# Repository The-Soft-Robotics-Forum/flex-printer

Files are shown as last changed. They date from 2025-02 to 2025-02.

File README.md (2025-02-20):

# Flex Printer

The Flex Printer is an open-source project aimed at solving the key print reliability difficulties associated with printing ultra-flexible elastomers (i.e. shore hardness of around 80A and below). It is based on the [Voron 0.2](https://github.com/VoronDesign/Voron-0) frame and motion system, but has been heavily modified, and stripped down to remove unnecessary parts; the resulting assembly is much easier to build and use, especially for newcomers to the field.

The project is aimed at providing a democratised platform for carrying out research in soft robotics involving the printing of soft elastomers (e.g. for fluidic soft robots).
The printer can be built for less than $500, with the total assembly time estimated at 1-3 days for first-time users (and under 1 day for those with prior experience).

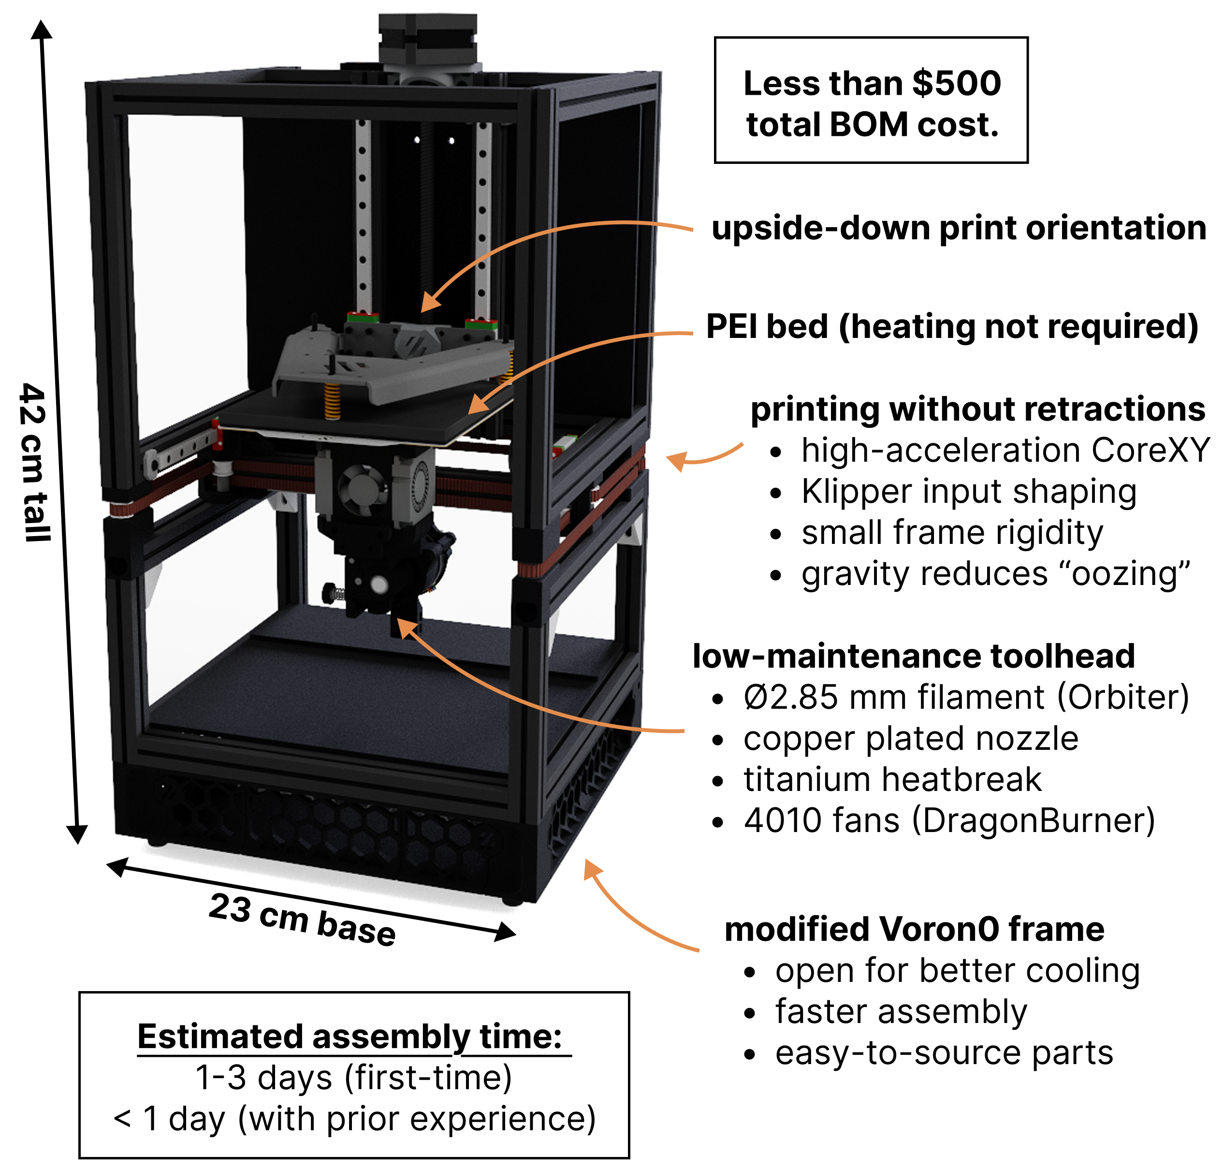
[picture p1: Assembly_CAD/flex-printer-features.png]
The key features of the Flex Printing platform


## Table of Contents
* [Overarching philosophy](#overarching-philosphy)
* [Key features](#key-features)
* [Printing impossible geometries](#printing-previosly-unfeasible-geometries)
* [Getting started](#getting-started)
* [Join the official Discord channel](#join-the-official-discord-channel)
* [How to contribute](#how-to-contribute)

## Overarching philosophy
The original Voron printers are very fun to build, but can be an arduous process for first-time builders; it is a platform designed primarily with hobbyists in mind. The Flex Printer has been optimised to simplify the assembly and usage of the printer as much as possible. The guidance provided in this repository aims to prevent future users of the platform from having the face the same challenges that the authors had to face when building Voron printers. The project follows a Keep It Simple, Stupid (KISS) philosophy, omitting decorative elements and any parts deemed unnecessary. These can, of course, be added back by the users to customise their builds.

## Key features

- Upside-down print orientation
    - Stabilises thin membranes during printing, and helps to keep them airtight (key for printing fluidic soft robots).
    - Allows to print arbitrarily tall slender structures (such as walls and columns). It is now possible to print geometries which previously would have collapsed under their own weight.
    - Enables better bridging and minimises the risk of blockage of fluidic channels (enabling to build more tightly integrated fluidic architectures).
    - Enables to suspend parts on thin strands of filament ("aero supports"), and print parts in virtually any print orientation.
- The printer can print parts in virtually any orientation
    - (Using "aero" support, as explained in the previous point).
    - Unlocks possibilities for creating entirely new types of fluidic machines, soft robots, and metamaterials.
- Low-maintenance, modified extruder
    - Use of 2.85 mm filament, which is 7 times harder to buckle than 1.75 mm.
    - Eliminates the issue of flexible filament tangling itself around extruder gears.
    - The larger cross section allows to generate more force, and gives more control over how the filament is pushed out of the nozzle.
    - Increased maximum printing speeds.
    - Copper-plated nozzle and titanium alloy heatbreak minimise the risk of clogged nozzles.
- Heat bed completely removed to simplify assembly, and operation
    - TPU provides excellent adhesion to the PEI textured sheet, even in the upside-down orientation.
- Open-frame design
    - The lack of enclosure allows for better cooling and significantly simplifies the assembly.
- Compact and portable
    - The printer fits on any desktop (42 x 23 x 23 cm footprint).
    - It can be easily transported, and used even at remote locations, which unlocks new applications.
    - The 120x120x120 mm build volume is sufficient given the current scale of fluidic soft systems. Future development may involve the creation of larger printer size variants.
- Printing without retractions
    - Printing upside down minimises filament oozing.
    - Printing at high accelerations and travel speeds minimises the need for retraction; made possible through CoreXY + Klipper input shaping + small rigid frame. 

## Printing previosly unfeasible geometries
[![Demonstration of printer capabilities]()](https://vimeo.com/1057922438/d0713f3f35)

## Getting started
- Follow the part sourcing guide in the [BOM_Sourcing_Guide](https://github.com/The-Soft-Robotics-Forum/flex-printer/tree/main/BOM_Sourcing_Guide) folder to procure the parts needed to build the printer.
- If your BOM doesn't include all of the required parts, print the remaining ones using the resources available in the [Print_These_Parts](https://github.com/The-Soft-Robotics-Forum/flex-printer/tree/main/Print_These_Parts) folder.
- Follow the build instructions in the [Build_Instructions](https://github.com/The-Soft-Robotics-Forum/flex-printer/tree/main/Build_Instructions) folder to build the printer and get it ready for printing your first parts.
- Visit the [Fluidic Machine Bestiary](https://github.com/The-Soft-Robotics-Forum/fluidic-machine-bestiary) for a repository of ready-to-print monolithic robots. The Bestiary also contains an expanding library of fluidic control, actuator, and sensor components that use can use to build your own, entirely new, soft robots.

## Join the official Discord channel
We have set up a dedicated [Discord channel](https://discord.gg/4RNmUT7A5G) on the Soft Robotics Forum server. It's a great way to ask for help and advice when assembling and using the printer, as well as to connect with other members of the community, and start contributing your own ideas to the project.

## How to contribute
This is a beginner guide for forking github repositories and contributing to project. If you have prior experience, skip to [Step 6](#step-6:-pull-request). If you plan to contribute to the project, keep in mind that it is under the same license as the standard Voron printers; please see the LICENSE file for full details.
### Step 1: Fork the repo
1. Click the "Fork" button in the top-right corner of the page - [1](https://www.freecodecamp.org/news/how-to-fork-a-github-repository/).
2. Chose where to fork the repository.
### Step 2: Clone your forked repo
1. Go to your forked repo and copy the URL that appears when the green code button is clicked. 
2. Open a terminal on your computer and run `git clone [URL]` [2](https://www.gitkraken.com/learn/git/problems/github-how-to-fork).
### Step 3: Create a branch 
1. Navigate to your recently cloned repo on your pc via terminal.
2. `git checkout -b [NEW_BRANCH_NAME]` where new_branch_name is the name you wish to give your branch.
### Step 4: Make changes 
1. Make your desired changes to the part files keep note of the voron naming scheme and be consistent.
2. Run `git add .`
3. Run `git commit -m "a detailed message of the changes you have made"`
### Step 5: Push changes and create a pull request
1. `git push origin [NEW_BRANCH_NAME]`
2. Go to your fork on the github website and select compare and pull request.
3. Fill in the pull request details.
### Step 6: Pull request
- Provide a clear and concise title for the pull request.
- Include a detailed description of the part changes you have made and why.
	- If you have introduced new parts make sure the naming is consistent with the in place naming scheme.
	- If you have introduced new hardware please provide a BOM for this.

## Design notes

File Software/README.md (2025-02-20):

# FLEX PRINTER ORCA INSTALL GUIDE 

## Step 1 
- Install the latest release of OrcaSlicer from their github releases page if you have not done so: [Orca Github](https://github.com/SoftFever/OrcaSlicer/releases_)

## Step 2 
- Select the preview tab, go to printer drop down, and select `Select/Remove printers(system presets)`
    - if this is your first install of orcaslicer the page will likely look a little different, but the steps are much the same 

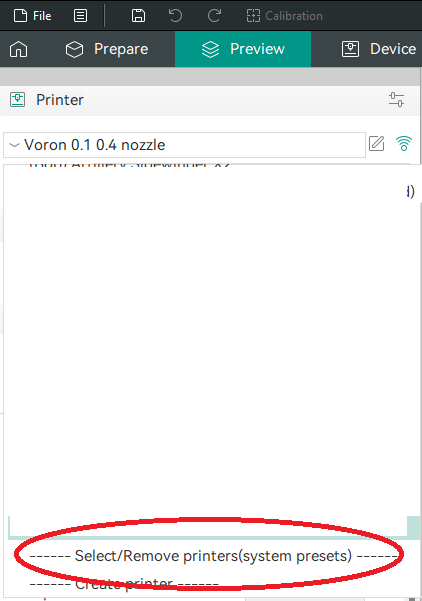
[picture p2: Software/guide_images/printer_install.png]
printer


## Step 3 
- Enter `Voron` into the search 
- Select the Voron 0.1 with 0.4 mm nozzle (or whatever nozzle size you have installed) 
- Press Confirm

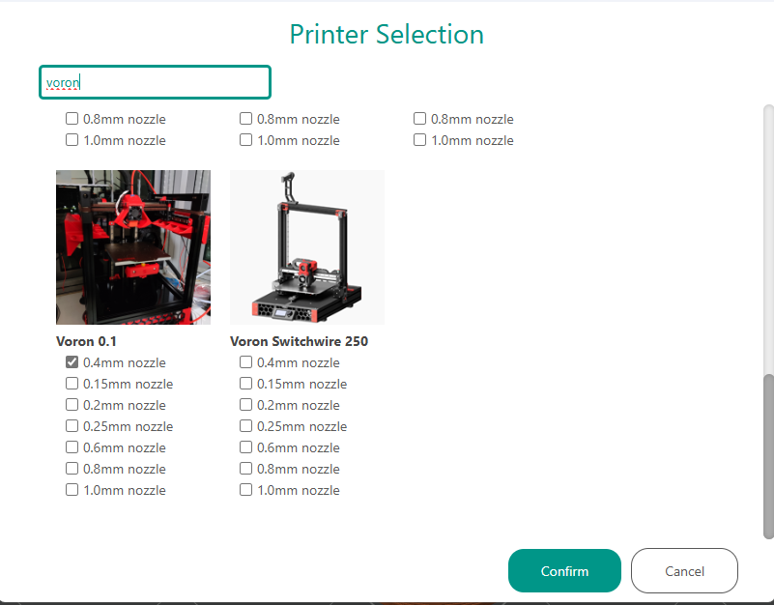
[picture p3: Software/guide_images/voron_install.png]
voron


## Step 4
- Ensure the Voron is selected in the drop down
- In the top left of the screen go to file/import/import configs...
- Locate the `orca_slicer_presets.orca_printer` file available [here](https://github.com/The-Soft-Robotics-Forum/flex-printer/blob/main/Software/orca_slicer_presets.orca_printer)
- This will make the Flex Printer presets available as options on the voron printer model 

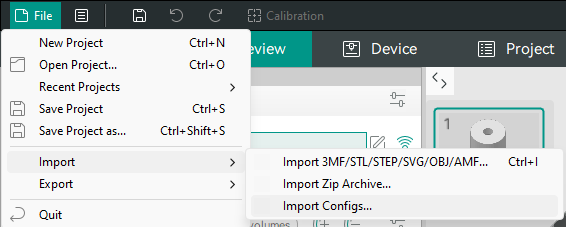
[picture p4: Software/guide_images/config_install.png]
config


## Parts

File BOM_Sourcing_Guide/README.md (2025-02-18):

# Bill of Materials (BOM) and sourcing guide
The included spreadsheet file contains our recommendations for the parts to purchase for the build. We will provide a couple of alternatives, as well as Aliexpress links so that they can be easily sourced globally. Note the pricess fluctuate rapidly on Ali, there are also variations in exchange rates. You might be able to find a better deal from one of the local suppliers on your country (e.g. [OneTwo3D](https://www.onetwo3d.co.uk/) in the UK, or [3DJake](https://www.3djake.uk/) in Germany & rest of EU).

### Finding the best BOM option for you
One of the easiest ways to source the printer parts is to actually buy one of the pre-made kits from brands like LDO, Siboor, Formbot, FYSETC. Note that when ordering a kit, you will be throwing away half of the parts since we don't need them, but you will also have more spares of others. Some kits come with a surplus of the printed parts, so this might be the option for you if you don't have another printer to print them.

The ranking of differences in quality between these brands is a subject of widespread discussion amongst Voron community members, but the general consensus appears to be that LDO is by far the highest quality, Siboor is OK and much cheaper, Formbot and FYSETC are the cheapest, but can be hit or miss, i.e. you might get lower quality parts, with worse tolerances. Lower part quality might limit your machine's performance and reliability slightly, but comes with the benefit of a lower price point.

Buying a Siboor/Formbot/FYSETC kit + any remaining parts is probably the easiest way to get below the $500 price point. One of the goals of the project is to further refine this sourcing process to make it as easy as possible; this might involve a custom kit specifically for this printer, or some new custom parts which simplify the assembly and reduce the cost even further.

A good middle ground for now can be sourcing LDO parts for the components which affect the performance the most (in order of importance: the linear rails, motors, frame extrusions, nozzles), though this might result in going slightly above the $500 price point depending on where you are ordering from, the fluctuating prices and currency exchange rates, etc.

### Electronics
The default for electronics is using a Raspberry Pi3B/3B+ or newer, but you could also use a Pi Zero 2W to further reduce the price point; this does come with some caveats though, and the regular Pi makes it easier to add further addons like webcams using USB, so we recommend this option. The are also boards that remove the need for a separate Pi running Klipper + MCU board, like the Fly Gemini 3.0 board with which some kits like Siboor come packaged with. This can be convenient, but OP has seen that there can sometimes be mysterious issues with these boards (or they work perfectly fine...). The Pi + SKR Pico combo is the safe choice if you want to make sure you don't run into issues later.

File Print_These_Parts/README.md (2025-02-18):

# Printed part directory
If you don't decide to build the printer using a kit that comes with all of the printed (or CNC'd) parts, you will need to print them yourself. Since the assembly has been heavily simplified, there aren't that many parts left to print.

The "Ready_To_Print_Prearranged" folder comes with preset plates that you can load into your slicer, and go. The .3mf file also includes the default recommended settings for FDM:
* 0.2mm layer height
* 0.4mm forced extrusion width
* Infill types: either grid, gyroid, honeycomb, triangle or cubic
* 40% infill percentage
* 4 perimeters (walls)
* 5 top/bottom solid layers.

For the material, the recommendation is always ABS/ASA as other materials like PLA can degrade and crack, especially when under temperature. Since we are not using an enclosure and heated bed, you could possibly get away with it, but we highly recommend sticking with ABS/ASA to avoid issues.

You can also use the Voron community Print It Forward (PIF) scheme to pay community members located near you to print and ship the parts to you. To find out more, visit https://pif.voron.dev/

# Part file naming guide
The "Individual_STL" files contains all the separate STL files, in case you want to slice and print them separately.

**QUANTITY REQUIRED**

*Thumb_Nut_x3.stl*  
Any file that ends with “_x#” is telling you the quantity of that part required to build the machine.

**FYI: ACCENT COLOR**

*[a]_Tensioner_Knob_x2.stl*  
The original Voron files use the "[\a]" prefix to indicate the part should be printed with a coloured accent (and "[\c]" for clear parts). This is unnecessary, and just complicates the overall build process, so we recommend printing all parts in one colour. Noting it here to indicate what it means in the original Voron naming scheme that you might notice being used if reusing parts from other repositories.

# Optional files
The "[\Optional]_Extra_or_Alternative_Parts" folder contains optional addons, adapters for alternative electronics boards, etc. You do not need to print these for the stock build.

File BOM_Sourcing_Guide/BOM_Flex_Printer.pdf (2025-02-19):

Category | Item | Qty. Price (GBP) Subtotal (GBP) | Link | Comments
Formbot Kit Kit options Siboor Kit FYSETC Kit | 1 0 0 | £275.19 £275.19 £317.92 £0.00 £359.59 £0.00
Aluminum Bed, 120x120x6mm Print bed Kirigami Bed | 0 0 0 | £12.09 £0.00 £5.69 £0.00 £10.18 £0.00
BTT SKR Pico | 0 | £15.24 £0.00
Electronics | Raspberry Pi 3B or newer | 0 | £33.99 | £0.00 | You might be able to source for cheaper elsewhere, or have one lying around. (https://www.aliexpress.com/item/1005005686303304.html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)
| MicroSD Card, 16G or more | 1 | £2.34 | £2.34 | Kit might also include this (https://www.aliexpress.com/item/1005007498193121.html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)
Umbillical PCB | 0 | £10.29 £0.00
Fans 4010 blower fan, dual ball GDSTIME | 2 | £10.69 £21.38
D2F-5 end stop switch | 0 | £0.52 | £0.00 | You can grab spares. (https://www.aliexpress.com/item/1005005204376959.html)
Axial Fan, 3010, 24V | 0 | £7.44 | £0.00 | The kits should have 2 of these, but double check (https://www.aliexpress.com/item/1005001793269882.html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)
Extruder 3.0 mm titanium heatbreak V6 heatsink 3.0 mm Heater + thermistor 2.85 mm drive gear kit TriangleLab | 1 1 1 1 | £4.34 £4.34 £3.24 £3.24 £3.51 £3.51 £13.29 £13.29
Orbiter V1.5 hardware + LDO motor | 0 | £28.79 £0.00
Hotend sock V6 plated copper block trianglelab | 1 1 | £2.16 £2.16 £9.79 £9.79
Power Mains switch | 0 | £1.12 £0.00
Orbiter V1.5 hardware, no motor | 1 | £12.29 | £12.29 | Note the Orbiter 1.5 has a different footprint from the F2.85, so our extruder printed part has a slight spacer to accommodate (https://www.aliexpress.com/item/1005002278201831.html) the injection molded part.
Orbiter F2.85 LDO prebuilt | 0 | £46.59 | £0.00 | The kits come with the stepper motor, but by buying this part you won’t need to print the parts (https://www.aliexpress.com/item/1005002781074910.html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)
LRS-100-24 power supply | 0 | £15.69 | £0.00 | Stock kit comes with 150W or more but we’re not using a heated bed. 100W should be more than enough, but you (https://www.aliexpress.com/item/4000417108777.html) can always get a bigger one.

Other

Siboor Hardware Kit | 0 | £22.59 | £0.00 | This has plenty of spare fasteners as well, but you could use more M3x10 and M3x50 (https://www.aliexpress.com/item/1005004195409464.html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)
M3x10 BHCS (50 pcs) | 1 | £1.15 | £1.15
M3x50 (any hex, 10pcs) | 1 | £1.60 | £1.60
6mm gates belt (4M length) | 0 | £7.82 | £0.00 | You can grab longer length to have spares (https://www.aliexpress.com/item/32853559638.html)
Corner brackets x 4 | 1 | £4.39 | £4.39 | For fixing bottom third of frame (i.e. former tophat) to the rest of the body. You can also use other fasteners, or print your (https://www.aliexpress.com/item/1005002337390401.html) own attachment.

If not getting a kit

Frame kit | 0 | £43.79 | £0.00 | If you can find the LDO kit somewhere else, it should be high quality. (https://www.aliexpress.com/item/1005004054773766.html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)
T nuts for rails | 0 | £10.49 | £0.00
LDO motor kit | 0 | £60.79 | £0.00
LDO linear rail kit | 0 | £69.95 | £0.00 | Couldn’t find on Ali (https://www.onetwo3d.co.uk/product/voron-0-linear-rail-kit-by-ldo/)
Set of panels (any should do, can procure for much cheaper) | 0 | £19.99 | £0.00 | Couldn’t find on Ali (https://www.onetwo3d.co.uk/product/linneo-voron-0-2-deck-back-panels-acm/)
TOTAL | £354.67

### Legend

Required
Not required
Different options you can opt for https://www.aliexpress.com/item/1005007863277974.html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 https://www.aliexpress.com/item/1005005295642824.html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 https://www.aliexpress.com/item/1005005338161717.html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 https://www.aliexpress.com/item/1005004428776917.html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
Spring Steel Flex Plate, 120x120mm, PEI Textured + smooth | https://www.aliexpress.com/item/1005005551646331.html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 https://www.aliexpress.com/item/1005005913879717.html?spm=a2g0o.order_list.order_list_main.386.24d01802XzWiW8 https://www.aliexpress.com/item/1005005686303304.html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 https://www.aliexpress.com/item/1005006043530249.html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 https://www.aliexpress.com/item/1005007498193121.html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 https://www.aliexpress.com/item/1005004265151654.html?spm=a2g0o.order_list.order_list_main.341.44c2180236tlJw https://www.aliexpress.com/item/1005005204376959.html?spm=a2g0o.order_list.order_list_main.336.44c2180236tlJw https://www.aliexpress.com/item/32799324058.html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 https://www.aliexpress.com/item/1005001793269882.html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 https://www.aliexpress.com/item/4000057995088.html?spm=a2g0o.order_list.order_list_main.360.24d01802XzWiW8 https://www.aliexpress.com/item/1005003064205906.html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 https://www.aliexpress.com/item/32849251623.html?spm=a2g0o.order_detail.order_detail_item.11.29e5f19cB9587U https://www.aliexpress.com/item/32950159362.html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 https://www.aliexpress.com/item/1005002278201831.html?spm=a2g0o.order_list.order_list_main.5.433c1802csn2bN https://www.aliexpress.com/item/1005002278201831.html?spm=a2g0o.order_list.order_list_main.5.433c1802csn2bN https://www.aliexpress.com/item/1005002781074910.html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 https://www.aliexpress.com/item/32916210903.html?spm=a2g0o.order_list.order_list_main.281.44c2180236tlJw https://www.aliexpress.com/item/4000011928654.html?spm=a2g0o.order_list.order_list_main.363.44c2180236tlJw https://www.aliexpress.com/item/1005005173695637.html?spm=a2g0o.order_list.order_list_main.346.44c2180236tlJw https://www.aliexpress.com/item/4000417108777.html?spm=a2g0o.order_list.order_list_main.351.44c2180236tlJw https://www.aliexpress.com/item/1005004195409464.html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 https://www.aliexpress.com/item/1005008064515476.html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 https://www.aliexpress.com/item/4000282775348.html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 https://www.aliexpress.com/item/32853559638.html?spm=a2g0o.order_list.order_list_main.321.44c2180236tlJw https://www.aliexpress.com/item/1005002337390401.html?spm=a2g0o.order_list.order_list_main.301.44c2180236tlJw https://www.aliexpress.com/item/1005004054773766.html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 https://www.aliexpress.com/item/1005007163562504.html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 https://www.aliexpress.com/item/1005004932910282.html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 https://www.onetwo3d.co.uk/product/voron-0-linear-rail-kit-by-ldo/ https://www.onetwo3d.co.uk/product/linneo-voron-0-2-deck-back-panels-acm/

Category | Item | Qty. Price (GBP) Subtotal (GBP) | Link | Comments
Formbot Kit Kit options Siboor Kit FYSETC Kit | 0 0 0 | £275.19 £0.00 £317.92 £0.00 £359.59 £0.00
Aluminum Bed, 120x120x6mm Print bed Kirigami Bed | 1 1 1 | £12.09 £12.09 £5.69 £5.69 £10.18 £10.18
BTT SKR Pico MicroSD Card, 16G or more Umbillical PCB | 1 1 1 | £15.24 £15.24 £2.34 £2.34 £10.29 £10.29
Fans 4010 blower fan, dual ball GDSTIME Axial Fan, 3010, 24V | 2 2 | £10.69 £21.38 £7.44 £14.88
Extruder 3.0 mm titanium heatbreak V6 heatsink 3.0 mm Heater + thermistor | 1 1 1 | £4.34 £4.34 £3.24 £3.24 £3.51 £3.51
2.85 mm drive gear kit TriangleLab | 0 | £13.29 £0.00
Electronics | Raspberry Pi 3B or newer | 1 | £33.99 | £33.99 | You might be able to source for cheaper elsewhere, or have one lying around. (https://www.aliexpress.com/item/1005005686303304.html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)
D2F-5 end stop switch | 1 | £0.52 | £0.52 | You can grab spares. (https://www.aliexpress.com/item/1005005204376959.html)
Orbiter V1.5 hardware, no motor | 0 | £12.29 | £0.00 | Note the Orbiter 1.5 has a different footprint from the F2.85, so our extruder printed part has a slight spacer to accommodate (https://www.aliexpress.com/item/1005002278201831.html) the injection molded part.
Orbiter V1.5 hardware + LDO motor | 0 | £28.79 £0.00
Hotend sock V6 plated copper block trianglelab | 1 1 | £2.16 £2.16 £9.79 £9.79
Power Mains switch | 1 | £1.12 £1.12
M3x10 BHCS (50 pcs) Other M3x50 (any hex, 10pcs) Corner brackets x 4 | 1 1 1 | £1.15 £1.15 £1.60 £1.60 £4.39 £4.39
Orbiter F2.85 LDO prebuilt | 1 | £46.59 | £46.59 | The kits come with the stepper motor, but by buying this part you won’t need to print the parts (https://www.aliexpress.com/item/1005002781074910.html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)
LRS-100-24 power supply | 1 | £15.69 | £15.69 | Stock kit comes with 150W or more but we’re not using a heated bed. 100W should be more than enough, but you (https://www.aliexpress.com/item/4000417108777.html) can always get a bigger one.
Siboor Hardware Kit | 1 | £22.59 | £22.59 | This has plenty of spare fasteners as well, but you could use more M3x10 and M3x50 (https://www.aliexpress.com/item/1005004195409464.html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)
6mm gates belt (4M length) | 1 | £7.82 | £7.82 | You can grab longer length to have spares (https://www.aliexpress.com/item/32853559638.html)

If not getting a kit

Frame kit | 1 | £43.79 | £43.79 | If you can find the LDO kit somewhere else, it should be high quality. (https://www.aliexpress.com/item/1005004054773766.html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)
T nuts for rails | 1 | £10.49 | £10.49
LDO motor kit | 1 | £60.79 | £60.79
LDO linear rail kit | 1 | £69.95 | £69.95 | Couldn’t find on Ali (https://www.onetwo3d.co.uk/product/voron-0-linear-rail-kit-by-ldo/)
Set of panels (any should do, can procure for much cheaper) | 1 | £19.99 | £19.99 | Couldn’t find on Ali (https://www.onetwo3d.co.uk/product/linneo-voron-0-2-deck-back-panels-acm/)
TOTAL | £455.60

### Legend

Required
Not required
Different options you can opt for https://www.aliexpress.com/item/1005007863277974.html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 https://www.aliexpress.com/item/1005005295642824.html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 https://www.aliexpress.com/item/1005005338161717.html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 https://www.aliexpress.com/item/1005004428776917.html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
Spring Steel Flex Plate, 120x120mm, PEI Textured + smooth | https://www.aliexpress.com/item/1005005551646331.html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 https://www.aliexpress.com/item/1005005913879717.html?spm=a2g0o.order_list.order_list_main.386.24d01802XzWiW8 https://www.aliexpress.com/item/1005005686303304.html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 https://www.aliexpress.com/item/1005006043530249.html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 https://www.aliexpress.com/item/1005007498193121.html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 https://www.aliexpress.com/item/1005004265151654.html?spm=a2g0o.order_list.order_list_main.341.44c2180236tlJw https://www.aliexpress.com/item/1005005204376959.html?spm=a2g0o.order_list.order_list_main.336.44c2180236tlJw https://www.aliexpress.com/item/32799324058.html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 https://www.aliexpress.com/item/1005001793269882.html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 https://www.aliexpress.com/item/4000057995088.html?spm=a2g0o.order_list.order_list_main.360.24d01802XzWiW8 https://www.aliexpress.com/item/1005003064205906.html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 https://www.aliexpress.com/item/32849251623.html?spm=a2g0o.order_detail.order_detail_item.11.29e5f19cB9587U https://www.aliexpress.com/item/32950159362.html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 https://www.aliexpress.com/item/1005002278201831.html?spm=a2g0o.order_list.order_list_main.5.433c1802csn2bN https://www.aliexpress.com/item/1005002278201831.html?spm=a2g0o.order_list.order_list_main.5.433c1802csn2bN https://www.aliexpress.com/item/1005002781074910.html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 https://www.aliexpress.com/item/32916210903.html?spm=a2g0o.order_list.order_list_main.281.44c2180236tlJw https://www.aliexpress.com/item/4000011928654.html?spm=a2g0o.order_list.order_list_main.363.44c2180236tlJw https://www.aliexpress.com/item/1005005173695637.html?spm=a2g0o.order_list.order_list_main.346.44c2180236tlJw https://www.aliexpress.com/item/4000417108777.html?spm=a2g0o.order_list.order_list_main.351.44c2180236tlJw https://www.aliexpress.com/item/1005004195409464.html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 https://www.aliexpress.com/item/1005008064515476.html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 https://www.aliexpress.com/item/4000282775348.html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 https://www.aliexpress.com/item/32853559638.html?spm=a2g0o.order_list.order_list_main.321.44c2180236tlJw https://www.aliexpress.com/item/1005002337390401.html?spm=a2g0o.order_list.order_list_main.301.44c2180236tlJw https://www.aliexpress.com/item/1005004054773766.html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 https://www.aliexpress.com/item/1005007163562504.html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 https://www.aliexpress.com/item/1005004932910282.html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 https://www.onetwo3d.co.uk/product/voron-0-linear-rail-kit-by-ldo/ https://www.onetwo3d.co.uk/product/linneo-voron-0-2-deck-back-panels-acm/

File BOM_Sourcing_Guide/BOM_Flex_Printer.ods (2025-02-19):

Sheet: Cheapest (Kit + remaining parts)
Category | Item | Qty. | Price (GBP) | Subtotal (GBP) | Link | Comments
Kit options | Formbot Kit | 1 | £275.19 | £275.19 | https://www.aliexpress.com/item/1005007863277974.html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
 | Siboor Kit | 0 | £317.92 | £0.00 | https://www.aliexpress.com/item/1005005295642824.html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
 | FYSETC Kit | 0 | £359.59 | £0.00 | https://www.aliexpress.com/item/1005005338161717.html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
Print bed | Aluminum Bed, 120x120x6mm | 0 | £12.09 | £0.00 | https://www.aliexpress.com/item/1005004428776917.html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
 | Spring Steel Flex Plate, 120x120mm, PEI Textured + smooth | 0 | £5.69 | £0.00 | https://www.aliexpress.com/item/1005005551646331.html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
 | Kirigami Bed | 0 | £10.18 | £0.00 | https://www.aliexpress.com/item/1005005913879717.html
Electronics | Raspberry Pi 3B or newer | 0 | £33.99 | £0.00 | https://www.aliexpress.com/item/1005005686303304.html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 | You might be able to source for cheaper elsewhere, or have one lying around.
 | BTT SKR Pico | 0 | £15.24 | £0.00 | https://www.aliexpress.com/item/1005006043530249.html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
 | MicroSD Card, 16G or more | 1 | £2.34 | £2.34 | https://www.aliexpress.com/item/1005007498193121.html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 | Kit might also include this
 | Umbillical PCB | 0 | £10.29 | £0.00 | https://www.aliexpress.com/item/1005004265151654.html
 | D2F-5 end stop switch | 0 | £0.52 | £0.00 | https://www.aliexpress.com/item/1005005204376959.html | You can grab spares.
Fans | 4010 blower fan, dual ball GDSTIME | 2 | £10.69 | £21.38 | https://www.aliexpress.com/item/32799324058.html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
 | Axial Fan, 3010, 24V | 0 | £7.44 | £0.00 | https://www.aliexpress.com/item/1005001793269882.html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 | The kits should have 2 of these, but double check
Extruder | 3.0 mm titanium heatbreak | 1 | £4.34 | £4.34 | https://www.aliexpress.com/item/4000057995088.html
 | V6 heatsink 3.0 mm | 1 | £3.24 | £3.24 | https://www.aliexpress.com/item/1005003064205906.html
 | Heater + thermistor | 1 | £3.51 | £3.51 | https://www.aliexpress.com/item/32849251623.html
 | 2.85 mm drive gear kit TriangleLab | 1 | £13.29 | £13.29 | https://www.aliexpress.com/item/32950159362.html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
 | Orbiter V1.5 hardware, no motor | 1 | £12.29 | £12.29 | https://www.aliexpress.com/item/1005002278201831.html | Note the Orbiter 1.5 has a different footprint from the F2.85, so our extruder printed part has a slight spacer to accommodate the injection molded part.
 | Orbiter V1.5 hardware + LDO motor | 0 | £28.79 | £0.00 | https://www.aliexpress.com/item/1005002278201831.html
 | Orbiter F2.85 LDO prebuilt | 0 | £46.59 | £0.00 | https://www.aliexpress.com/item/1005002781074910.html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 | The kits come with the stepper motor, but by buying this part you won’t need to print the parts
 | Hotend sock | 1 | £2.16 | £2.16 | https://www.aliexpress.com/item/32916210903.html
 | V6 plated copper block trianglelab | 1 | £9.79 | £9.79 | https://www.aliexpress.com/item/4000011928654.html
Power | Mains switch | 0 | £1.12 | £0.00 | https://www.aliexpress.com/item/1005005173695637.html
 | LRS-100-24 power supply | 0 | £15.69 | £0.00 | https://www.aliexpress.com/item/4000417108777.html | Stock kit comes with 150W or more but we’re not using a heated bed. 100W should be more than enough, but you can always get a bigger one.
Other | Siboor Hardware Kit | 0 | £22.59 | £0.00 | https://www.aliexpress.com/item/1005004195409464.html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 | This has plenty of spare fasteners as well, but you could use more M3x10 and M3x50
 | M3x10 BHCS (50 pcs) | 1 | £1.15 | £1.15 | https://www.aliexpress.com/item/1005008064515476.html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
 | M3x50 (any hex, 10pcs) | 1 | £1.60 | £1.60 | https://www.aliexpress.com/item/4000282775348.html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
 | 6mm gates belt (4M length) | 0 | £7.82 | £0.00 | https://www.aliexpress.com/item/32853559638.html | You can grab longer length to have spares
 | Corner brackets x 4 | 1 | £4.39 | £4.39 | https://www.aliexpress.com/item/1005002337390401.html | For fixing bottom third of frame (i.e. former tophat) to the rest of the body. You can also use other fasteners, or print your own attachment.
If not getting a kit | Frame kit | 0 | £43.79 | £0.00 | https://www.aliexpress.com/item/1005004054773766.html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 | If you can find the LDO kit somewhere else, it should be high quality.
 | T nuts for rails | 0 | £10.49 | £0.00 | https://www.aliexpress.com/item/1005007163562504.html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
 | LDO motor kit | 0 | £60.79 | £0.00 | https://www.aliexpress.com/item/1005004932910282.html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
 | LDO linear rail kit | 0 | £69.95 | £0.00 | https://www.onetwo3d.co.uk/product/voron-0-linear-rail-kit-by-ldo/ | Couldn’t find on Ali
 | Set of panels (any should do, can procure for much cheaper) | 0 | £19.99 | £0.00 | https://www.onetwo3d.co.uk/product/linneo-voron-0-2-deck-back-panels-acm/ | Couldn’t find on Ali
 |  |  | TOTAL | £354.67
 |  |  | Legend
 |  |  |  | Required
 |  |  |  | Not required
 |  |  |  | Different options you can opt for

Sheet: Upper-mid-range (Non-kit + LDO parts)_2
Category | Item | Qty. | Price (GBP) | Subtotal (GBP) | Link | Comments
Kit options | Formbot Kit | 0 | £275.19 | £0.00 | https://www.aliexpress.com/item/1005007863277974.html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
 | Siboor Kit | 0 | £317.92 | £0.00 | https://www.aliexpress.com/item/1005005295642824.html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
 | FYSETC Kit | 0 | £359.59 | £0.00 | https://www.aliexpress.com/item/1005005338161717.html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
Print bed | Aluminum Bed, 120x120x6mm | 1 | £12.09 | £12.09 | https://www.aliexpress.com/item/1005004428776917.html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
 | Spring Steel Flex Plate, 120x120mm, PEI Textured + smooth | 1 | £5.69 | £5.69 | https://www.aliexpress.com/item/1005005551646331.html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
 | Kirigami Bed | 1 | £10.18 | £10.18 | https://www.aliexpress.com/item/1005005913879717.html
Electronics | Raspberry Pi 3B or newer | 1 | £33.99 | £33.99 | https://www.aliexpress.com/item/1005005686303304.html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 | You might be able to source for cheaper elsewhere, or have one lying around.
 | BTT SKR Pico | 1 | £15.24 | £15.24 | https://www.aliexpress.com/item/1005006043530249.html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
 | MicroSD Card, 16G or more | 1 | £2.34 | £2.34 | https://www.aliexpress.com/item/1005007498193121.html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
 | Umbillical PCB | 1 | £10.29 | £10.29 | https://www.aliexpress.com/item/1005004265151654.html
 | D2F-5 end stop switch | 1 | £0.52 | £0.52 | https://www.aliexpress.com/item/1005005204376959.html | You can grab spares.
Fans | 4010 blower fan, dual ball GDSTIME | 2 | £10.69 | £21.38 | https://www.aliexpress.com/item/32799324058.html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
 | Axial Fan, 3010, 24V | 2 | £7.44 | £14.88 | https://www.aliexpress.com/item/1005001793269882.html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
Extruder | 3.0 mm titanium heatbreak | 1 | £4.34 | £4.34 | https://www.aliexpress.com/item/4000057995088.html
 | V6 heatsink 3.0 mm | 1 | £3.24 | £3.24 | https://www.aliexpress.com/item/1005003064205906.html
 | Heater + thermistor | 1 | £3.51 | £3.51 | https://www.aliexpress.com/item/32849251623.html
 | 2.85 mm drive gear kit TriangleLab | 0 | £13.29 | £0.00 | https://www.aliexpress.com/item/32950159362.html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
 | Orbiter V1.5 hardware, no motor | 0 | £12.29 | £0.00 | https://www.aliexpress.com/item/1005002278201831.html | Note the Orbiter 1.5 has a different footprint from the F2.85, so our extruder printed part has a slight spacer to accommodate the injection molded part.
 | Orbiter V1.5 hardware + LDO motor | 0 | £28.79 | £0.00 | https://www.aliexpress.com/item/1005002278201831.html
 | Orbiter F2.85 LDO prebuilt | 1 | £46.59 | £46.59 | https://www.aliexpress.com/item/1005002781074910.html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 | The kits come with the stepper motor, but by buying this part you won’t need to print the parts
 | Hotend sock | 1 | £2.16 | £2.16 | https://www.aliexpress.com/item/32916210903.html
 | V6 plated copper block trianglelab | 1 | £9.79 | £9.79 | https://www.aliexpress.com/item/4000011928654.html
Power | Mains switch | 1 | £1.12 | £1.12 | https://www.aliexpress.com/item/1005005173695637.html
 | LRS-100-24 power supply | 1 | £15.69 | £15.69 | https://www.aliexpress.com/item/4000417108777.html | Stock kit comes with 150W or more but we’re not using a heated bed. 100W should be more than enough, but you can always get a bigger one.
Other | Siboor Hardware Kit | 1 | £22.59 | £22.59 | https://www.aliexpress.com/item/1005004195409464.html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 | This has plenty of spare fasteners as well, but you could use more M3x10 and M3x50
 | M3x10 BHCS (50 pcs) | 1 | £1.15 | £1.15 | https://www.aliexpress.com/item/1005008064515476.html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
 | M3x50 (any hex, 10pcs) | 1 | £1.60 | £1.60 | https://www.aliexpress.com/item/4000282775348.html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
 | 6mm gates belt (4M length) | 1 | £7.82 | £7.82 | https://www.aliexpress.com/item/32853559638.html | You can grab longer length to have spares
 | Corner brackets x 4 | 1 | £4.39 | £4.39 | https://www.aliexpress.com/item/1005002337390401.html
If not getting a kit | Frame kit | 1 | £43.79 | £43.79 | https://www.aliexpress.com/item/1005004054773766.html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 | If you can find the LDO kit somewhere else, it should be high quality.
 | T nuts for rails | 1 | £10.49 | £10.49 | https://www.aliexpress.com/item/1005007163562504.html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
 | LDO motor kit | 1 | £60.79 | £60.79 | https://www.aliexpress.com/item/1005004932910282.html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
 | LDO linear rail kit | 1 | £69.95 | £69.95 | https://www.onetwo3d.co.uk/product/voron-0-linear-rail-kit-by-ldo/ | Couldn’t find on Ali
 | Set of panels (any should do, can procure for much cheaper) | 1 | £19.99 | £19.99 | https://www.onetwo3d.co.uk/product/linneo-voron-0-2-deck-back-panels-acm/ | Couldn’t find on Ali
 |  |  | TOTAL | £455.60
 |  |  | Legend
 |  |  |  | Required
 |  |  |  | Not required
 |  |  |  | Different options you can opt for

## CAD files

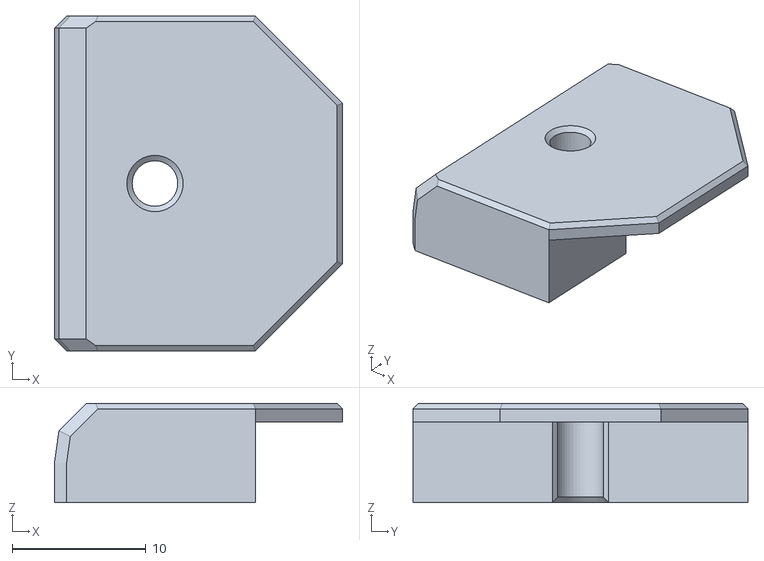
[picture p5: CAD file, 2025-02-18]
Print_These_Parts/Individual_STL/Electronics/Bottom_Panel_Clip_Taller_Longer_x2.stl
21.5 x 25.0 x 7.40

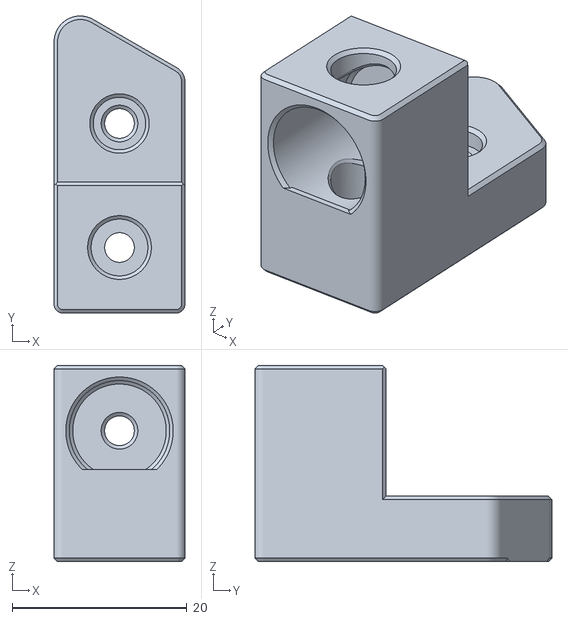
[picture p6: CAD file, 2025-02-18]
Print_These_Parts/Individual_STL/Motion/B_Idler_Upper_x1.stl
15.0 x 34.0 x 22.5

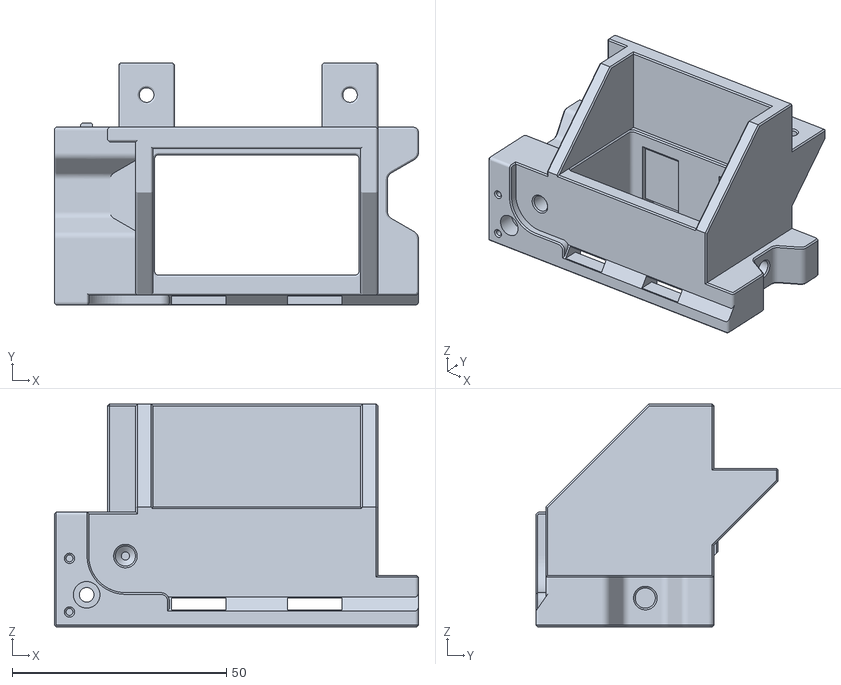
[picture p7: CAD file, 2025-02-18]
Print_These_Parts/Individual_STL/Skirts/Foot_Rear_Left_Power_Inlet_x1.STL
84.9 x 56.5 x 52.0

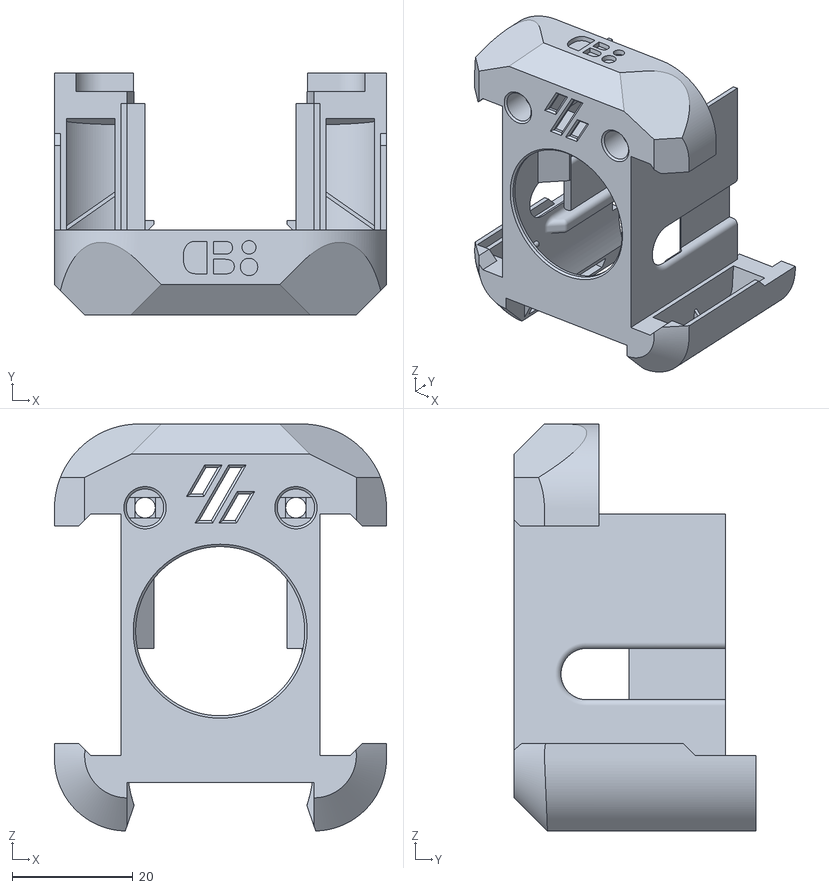
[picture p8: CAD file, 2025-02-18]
Print_These_Parts/Individual_STL/Toolhead/Toolhead_Cowl_Modified_x1.stl
55.0 x 40.0 x 67.4

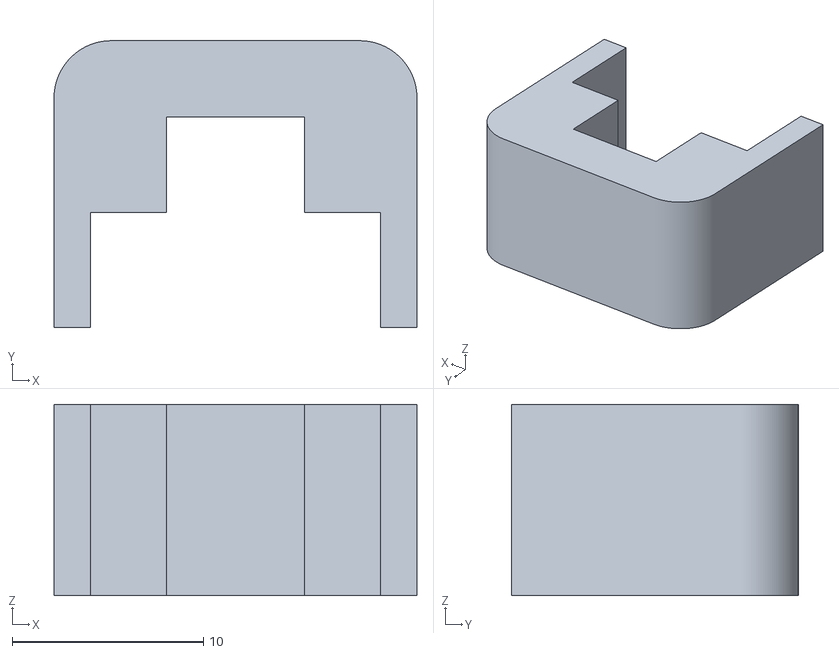
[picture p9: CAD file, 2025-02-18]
Print_These_Parts/Individual_STL/Tools/MGN7_Rail_Guide_x2.STL
19.0 x 15.0 x 10.0

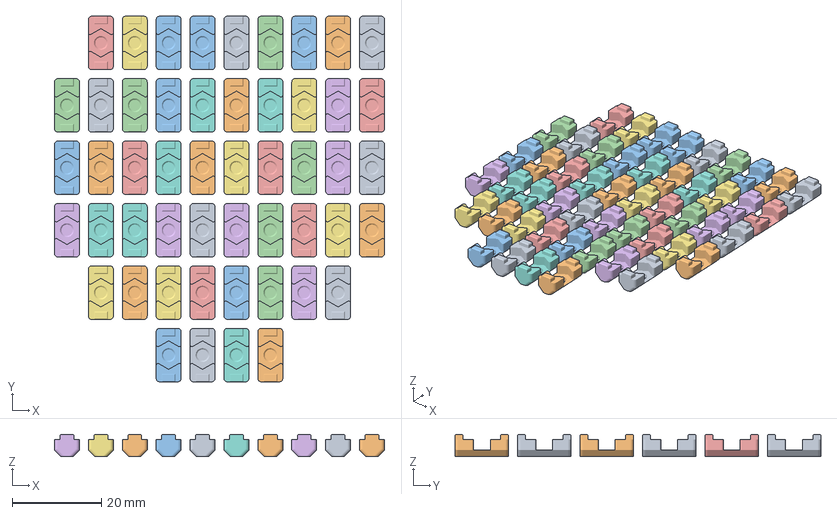
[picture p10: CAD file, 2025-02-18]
Print_These_Parts/Ready_To_Print_Prearranged/NoDropNuts_LDO_Extrusions_12mm_50pcs.3mf
74.0 x 82.0 x 5.00 mm
NoDropNut_12mm.stl x 51

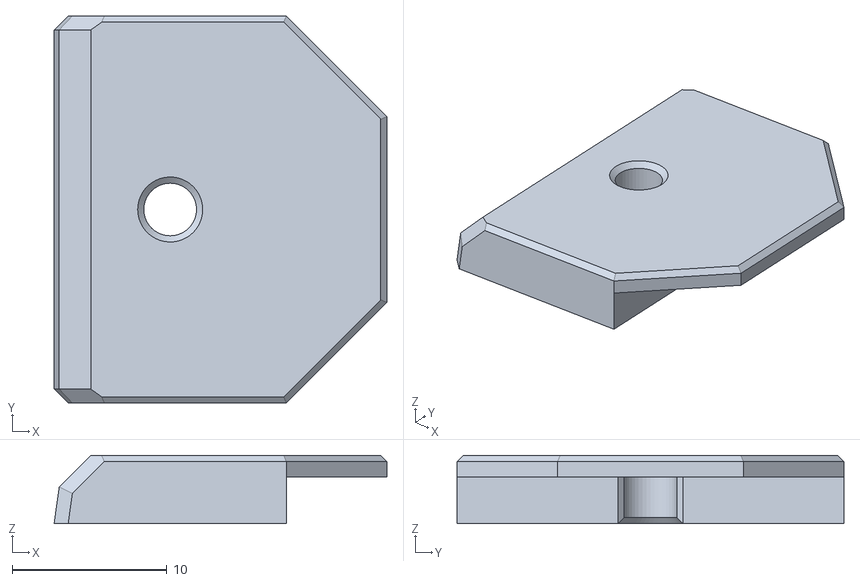
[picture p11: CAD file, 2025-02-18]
Print_These_Parts/Individual_STL/Electronics/Bottom_Panel_Clip_Longer_x1.stl
21.5 x 25.0 x 4.40

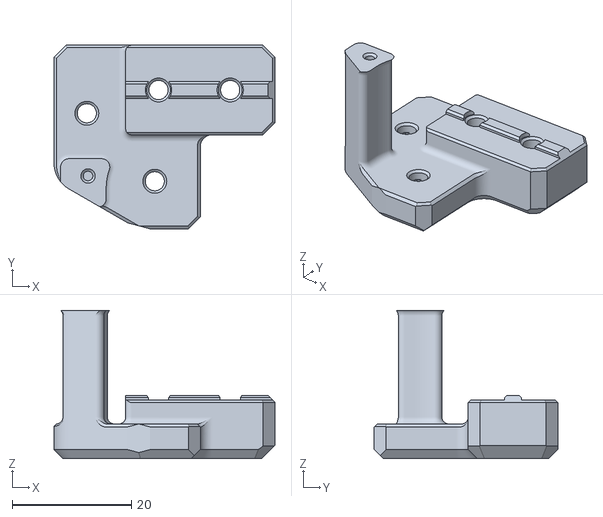
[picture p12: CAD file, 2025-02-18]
Print_These_Parts/Individual_STL/Motion/XY_Joint_Right_Upper_x1.stl
37.0 x 30.7 x 24.8

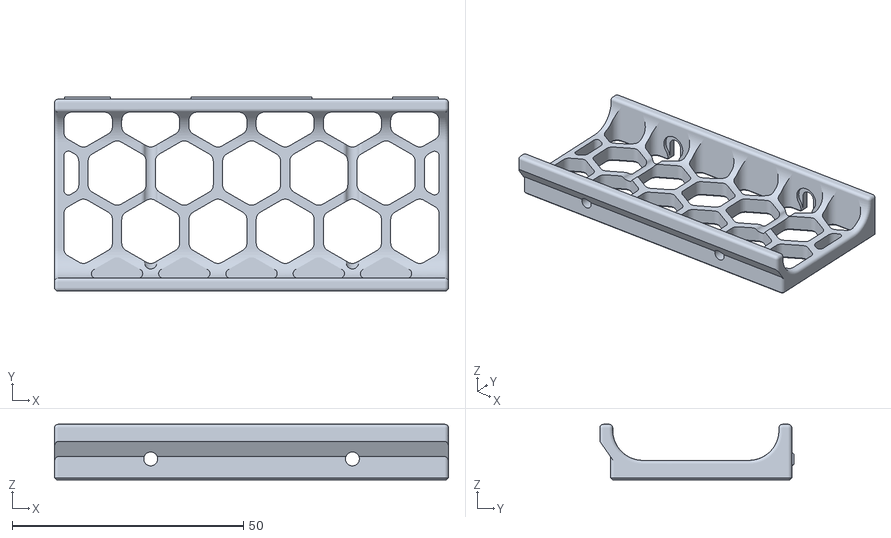
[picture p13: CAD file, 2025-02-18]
Print_These_Parts/Individual_STL/Skirts/Headless_Skirt_Insert_x1.STL
85.2 x 42.0 x 12.0

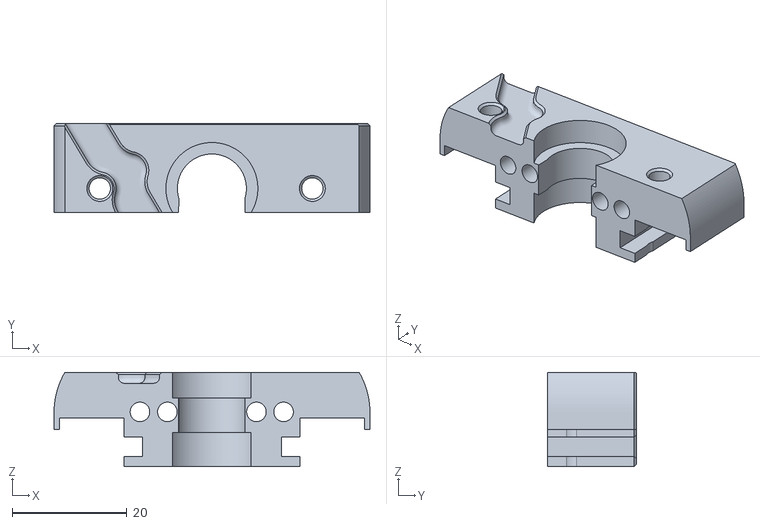
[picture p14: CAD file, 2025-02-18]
Print_These_Parts/Individual_STL/Toolhead/Toolhead_V6_Mount_Back_x1.stl
55.0 x 15.5 x 16.4

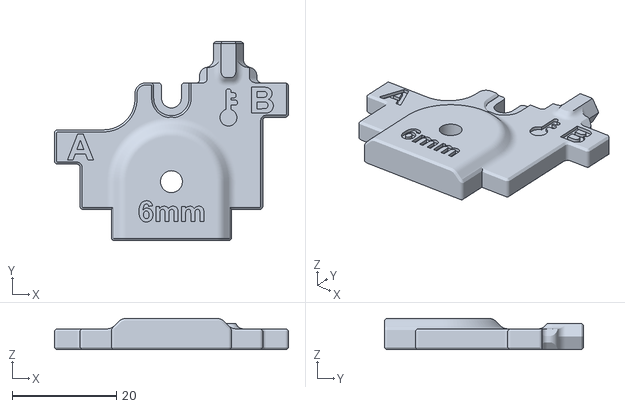
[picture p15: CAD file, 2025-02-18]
Print_These_Parts/Individual_STL/Tools/Swiss_Army_Jig_x1.STL
44.9 x 38.3 x 6.00

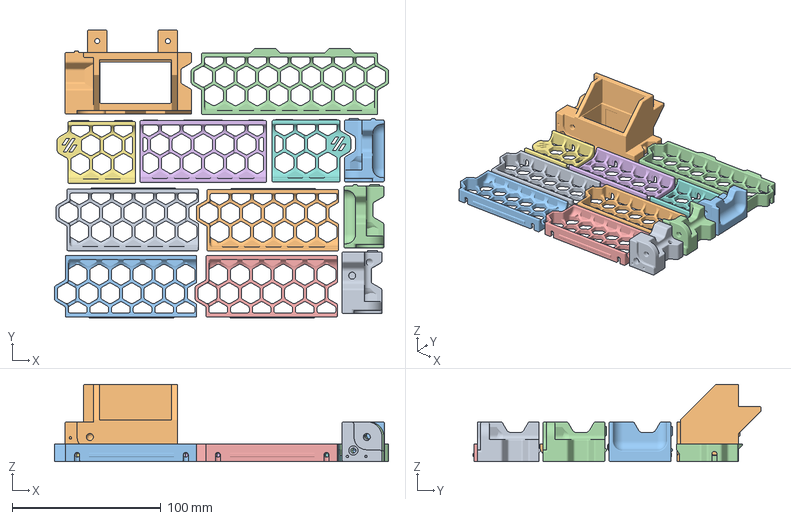
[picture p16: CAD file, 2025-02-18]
Print_These_Parts/Ready_To_Print_Prearranged/Skirts_Plate.3mf
224.4 x 193.5 x 52.0 mm
Side_Skirt_x2.STL x 2
Side_Skirt_Mirror_x2.stl x 2
Rear_Skirt_x1.STL
Headless_Skirt_Insert_x1.STL
Front_Skirt_B_x1.STL
Front_Skirt_A_x1.STL
Foot_Rear_Right_x1.STL
Foot_Rear_Left_Power_Inlet_x1.STL
Foot_Front_Right_x1.STL
Foot_Front_Left_x1.STL

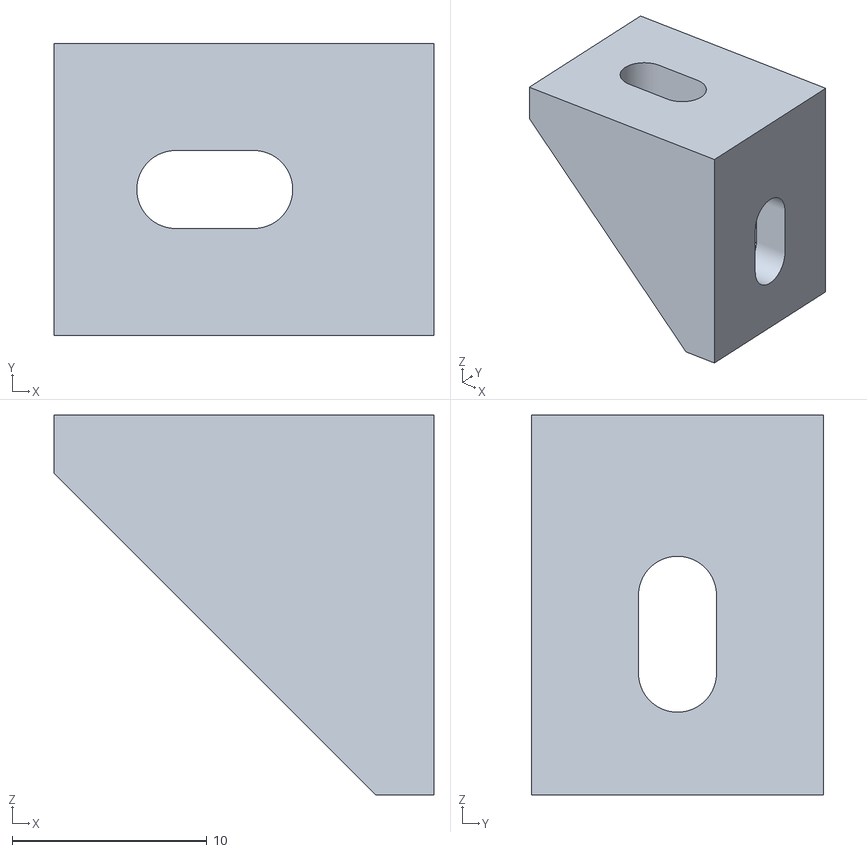
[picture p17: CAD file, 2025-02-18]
Print_These_Parts/[Optional]_Extra_or_Alternative_Parts/[Optional]_L_bracket_1515_x4.stl
19.5 x 15.0 x 19.5

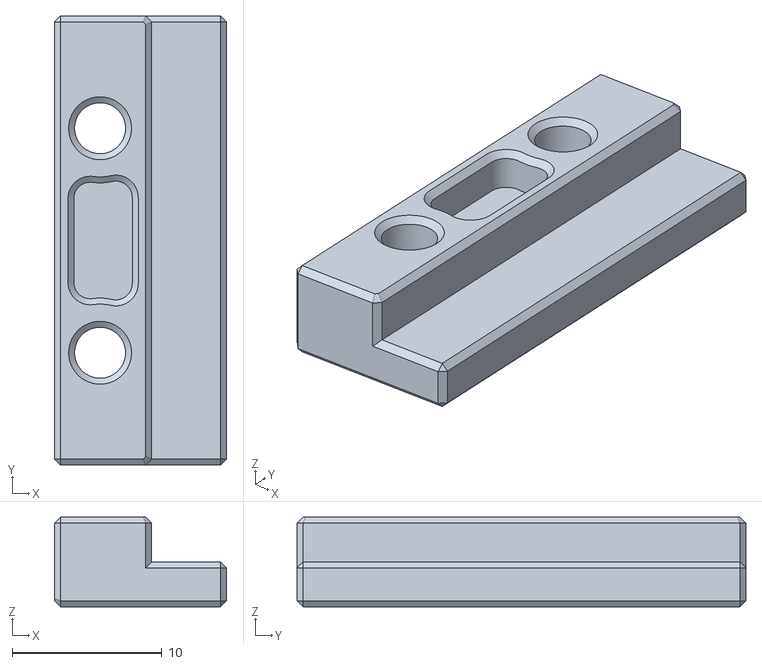
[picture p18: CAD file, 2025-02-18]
Print_These_Parts/Individual_STL/Electronics/Fan_Mount_Top_x1.stl
11.5 x 30.0 x 6.00

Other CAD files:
Assembly_CAD/Flex_Printer_Assembly.step
Print_These_Parts/[Optional]_Extra_or_Alternative_Parts/[Optional]_NoDropNuts_Fysetc_and_Other_Extrusions_12mm_50pcs.3mf
Print_These_Parts/Individual_STL/Motion/XY_Joint_Right_Lower_x1.stl
Print_These_Parts/Individual_STL/Skirts/Front_Skirt_A_x1.STL
Print_These_Parts/Individual_STL/Electronics/Bottom_Panel_Clip_Taller_x2.stl
Print_These_Parts/Individual_STL/Electronics/Bottom_Panel_Clip_x2.stl
Print_These_Parts/Individual_STL/Electronics/Fan_Mount_Bottom_x1.stl
Print_These_Parts/Individual_STL/Electronics/PCB_DIN_Clip_x2.stl
Print_These_Parts/Individual_STL/Electronics/PSU_Cover_x1.STL
Print_These_Parts/Individual_STL/Electronics/RPi_and_BTT-Pico_Mount_x2.STL
Print_These_Parts/Individual_STL/Electronics/Umbilical_PCB_Frame_Panel_x1.stl
Print_These_Parts/Individual_STL/Electronics/VHB_DIN_Mount_x2.STL
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

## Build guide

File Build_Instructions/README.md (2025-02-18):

# Build notes

This folder includes the original version of the Voron 0.2 assembly manual. Start by using those instructions, and consulting this README file to account for all of the differences from the stock build.

As the project evolves, a separate, dedicated version of the manual will be created. These assembly instructions will also be updated to account for changes introduced in the future, and to streamline the printer build process. Please also report any mistakes, things you found confusing, or general suggestions, by submitting them as Issues here on Github.

Note that we have also copied over some comments from the build notes of some associated repositories, like for some of the parts that come from the [LDO kit](https://docs.ldomotors.com/en/voron/voron02/build-faqv02r1), the [DragonBurner extruder](https://github.com/chirpy2605/voron/tree/main/V0/Dragon_Burner) assembly guide, etc.

# Comments relating to specific pages of the original assembly manual

### Core part of the assembly
* **Page 6** We have set up a dedicated channel on Discord, specifically for the Flex Printer. You can ask for help there. [Direct link to the channel](https://discord.gg/4RNmUT7A5G).
* **Page 7** Please make sure you log issues on the repo you are currently viewing, not the VoronDesign one. Otherwise, the repo mainteners won't be able to see them.
* **Page 12** Ignore if using our recommended BOM. It comes with pre-drilled extrusions.
* **Pages 13-15** Extrusions F & G are not included since the Kirigami bed will be used. The default-BOM extrusion ends should come pre-tapped.  As a result, Extrusions A & B are the same and Extrusions C & H are also the same.
* **Page 18** SKIP The kits include nut bars.
* **Page 19** Important: the linear rails need to be cleaned and lubed - you can refer to the [LDO Linear Rail Greasing Guide.](https://docs.ldomotors.com/en/guides/rail_grease_guide). **White lithium grease is the preferred choice of lubricant.** Be extra careful unwrapping with the rail that does not have the rubber stoppers, this is the HiWin rail for the x-axis.
* **Page 23** The no-drop nuts are incredibly useful. We have included a 50pc .3mf plate of these for the LDO extrusions. The Optional folder includes another version for extrusions that come with the FYSETC kit. The LDO ones are great, but in a few isolated locations they don't fit perfectly in a handfu(e.g. where the Z endstop is). You can just use regular nuts whenever this is the case.
* **Pages 36-46** 36-46 SKIP Use the [LDO Kirigami Bed Guide](https://www.ldomotion.com/p/guide/Kirigami-Bed-for-Voron-V02) for instructions.
	* Note we are not using the drag chain since there's no wires without the heated bed. Simplifies the wiring a fair bit as well. You're welcome.
	* So you also ignore all the other printed parts outside of the actual block for the Z nut.
* **Pages 47-48** The bed tramming is a notoriously unnerving experience, especially if the Kirigami bed comes delivered slightly out of shape. Try to get it as good as you can, but keep in mind it will never be perfect.
	* BTW if the Kirigami does come deformed, you can manually bend it to the required shape - the aluminium is quite pliable. Adjusting it ever so slightly can make tramming a whole lot easier.
	* Greg's Maker Corner on YouTube has a [good demo](https://youtu.be/r43oCBvVlFY?si=NVb_CkOZ1o9doB4y) of the tramming procedure.
* **Page 49** The manual still includes the old version of this parts (bolted from only one side), that's why it looks different. The updated one we have included will fit better.
* **Page 52** Comment on pre-loaded nuts in general: you won't need most of them because most of them are for clips for the enclosure, which we are not using.
	* We recommend still installing them according to the original guide, though, as they will make it easier to install any mods in the future.
	* An updated version of the guide coming soon will more clearly outline exactly which preloads you can definitely skip.
* **Page 58** Ignore both. We are not using the drag chain, and the deck panel will get installed elsewhere since we are going upside-down.
* **Page 62** See comment for Page 52 for notes about nut pre-loads.
* **Page 81** TIP: Insert your hex key into the holes thru the nut to pre-align the nuts into place.
* **Page 92** The Kirigami bed uses a different nut holder, this is the one we include with our printed files (see [LDO Kirigami Bed Guide](https://www.ldomotion.com/p/guide/Kirigami-Bed-for-Voron-V02) if in doubt). The spring and top part of the backlash nut does not attach until later.
* **Page 93** SKIP Not needed for Kirigami
* **Pages 94-95** You can safely ignore these since the open frame design allows to slide these in from the top at any point in the future.
* **Page 99** SKIP We won't be using the default spool holder; the position is not the best for the same reason as in the next comment.
* **Page 101** We won't be using the bowden fube or the filament runout sensor as it introduces extra friction on the TPU material and makes it harder to extrude.
* **Page 102** SKIP We will be att
* **Page 103** We are skipping the coloured accents so ignore these types of things throughout the whole manual.
* **Page 107** (If using the LDO kit or LDO leadscrew): Do NOT apply any lubricant on the leadscrew, it's Teflon coated.
* Page 110 Attach the top and spring on the backlash nut on this step, refer to the video on Page 108. This can be a little tricky to get the part to properly mesh and spring into place, so take your time.
* Page 112 This step is very critical, misalignment could cause permanent damage to the backlash nut or pre-mature excessive wear.
* **Page 122** Ignore, we are not using the cam locks.
* **Page 129** Leave a bit extra on top of this, so maybe like 1.1 m or so length in total. It will help with manually adjusting the belts to get the right tension.
* **Page 135** The Gates Carbon Drive app on iOS/Android is great for this. Make sure you are in a quiet environment and take the phone out of any case, hold microphone near belt.
	* If the belt is too loose you will find it hard to get any reading at all, that's what's going on. Tighten it a bit more until you start getting good readings, then you can reduce it if it's too high.
	* Usually go a bit higher than 110 Hz (even around 120Hz should be OK), since the belt will loosen a bit after it wears in, and over time later.
	* Refer to guide like [this one](https://docs.vorondesign.com/tuning/secondary_printer_tuning.html#belt-tension) if in doubt.
* **Page 136** Confusingly not stated in the original manual: if you alteady tightened the screws from Page 73, turning these knobs won't do anything. Generally you want to loosen these screws if we need to make major changes to the tension, and leave some room for finer adjustment later using the knobs.
* **Pages 139** SKIP We are using lock nuts instead to mitigate loosening over time.
* **Page 141-142** SKIP We are not using the heated bed.
* **Page 143** Use M3x30 instead (longer ones also work, but it will be annoying tightening the lock nut through the whole length).
	* You may also use extra lock nuts here (flat side up) instead of the nut and washer (i.e. in addition to the ones we use instead of the knobs).
* **Page 144** The bed from the BOM will already have this preapplied. Some might not have holes in the magnet sheet, though, so it's a bit harder to access later.
* **Page 146-148** SKIP You may now already be starting to see how removing the heated bed simplifies the assembly due to not having to deal with all the wiring.
* **Pages 150-177** SKIP We are using the DragonBurner extruder instead.
	* Use the [DragonBurner assembly manual](https://github.com/chirpy2605/voron/tree/main/V0/Dragon_Burner) to build that extruder instead.
	* FYI we are using the V6 mount + Orbiter 2 + custom Umbilical PCB mount combo.
	* Skip all the bits for the LEDs, unless you really need them. If in doubt, keep in mind you can also always take off the extruder later and replace it with a modified version.
	* **Page 178** comment: note that we are using M3x50mm, due to the need to attach the ADXL front mount.
* **Page 181** We recommend to zip tie the Umbillical cord to the long strain relief part of the PCB mount. Due to the position of the printer, the cord will be contacting the bottom deck panel, and can cause the wires to pull out slightly; this can cause significant temperature sensor noise and even abrupt print failures.
* **Page 182** You can ziptie 'em around the strain relief spacers. By the way, make sure the bit beside the fans doesn't stick out too much; it will push down on the belt anyway, but if it's too tight it can actually restrict toolhead movement and cause issues like layer shifting.
	* BTW, note that we are using the [Umbillical PCB](https://github.com/VoronDesign/Voron-Hardware/tree/master/V0-Umbilical) by default. It simplifies the wiring quite a bit as you will see. As mention in the BOM, in the future we will likely replace this for the new [Orbitool SO2](https://www.orbiterprojects.com/orbitools/). As that will just use one USB cable instead of the Umbillical cord, reducing the strain relief issue.
* **Page 197** Before we attach the wiring, we will use the extrusions meant for the tophat to build the bottom third of the printer frame. **Jump to page 229.**
* **Page 230** We will need preloads for the deck panels; check the CAD assembly to make sure you have enough nuts for all of the clips.
	* Note you won't need most of the other preloads in this chapter, but you can put them in anyway (for the same reason as in the comment for Page 52).
	* Consult the CAD assembly to get an idea of how the whole thing is going to look like, so you know into which rails you might want to load a few nuts later (on those J extrusions, since they won't be accessible).
	* The tophat bit of the frame can be freely detached later, though, so it's also not that big of a deal.
* **Page 232** SKIP We are not using the cam lock.
* **Page 232-240** SKIP We are not using the panels.

### Bottom third of the frame (reusing tophat extrusions)
You can now use the elbow brackets to attach the tophat frame to the bottom bit of the printer (i.e. on top of the XY motion system). See the CAD assembly if in doubt.
* Then, mount the deck panel(s), using the clips (again, see CAD assembly for now, we will update the guide in the future to illustrate this).
* **Now** we can finally attach the feet, like on Page 102. Again, ignore the coloured accents from Page 103.
* After attaching the power supply to the bottom of the deck panel you are ready to go through Pages 208 through 212 to attach the bottom skirts (ignoring coloured accent from 211).
	* TIP: You can partially thread the screws into the nuts first since the skirt can slide afterwards.

### Sorting out the electronics
After assembling the bottom bit of the frame, go back to sort out the electronics.
* It can be worth referring to the [LDO Wiring Guide](****). Even though our setup differs due to not using their Picobilical, the illustrated guide is very useful. We will make a custom wiring guide in the next version of the guide.
* **Page 201** Toolhead wires will go to the Umbillical PCB on the Toolhead. Then you route from the PCB attached on the frame to the actual controller board.
* **Page 204** Ignore, we are using the SKR Pico.
* **Page 212-216** SKIP We are indeed using the headless (i.e. non-display) variant. IMHO the display is not worth it and the cheap ones tend to be buggy. You just control the printer via web browser on your local network, and you can also use an app like OctoApp on your phone to control the printer.
* **Page 218** SKIP We are not routing the filament through there.
* **Page 219** We are installing the Umbillical frame PCB here using the panel provided with the STL files.
* **Pages 220 to 226** SKIP, we are purposefully omitting the panels.
	* You can probably now see why.

### Initial setup
Almost there! You can now go through the [original startup guide](https://docs.vorondesign.com/build/startup/) for all the pre-flight checks, bed levelling, and software setup.
* Note we are of course using only the sections for the Voron0.
* For the printer.cfg and macros.cfg files, use our presets from the "Software" folder of this repository.
* Due to using the lock nuts for the bed levelling adjustment, once you set it up initially, you won't need to re-adjust it for a long, long time.
* Once done, consider sharing a picture of your finalised Flex Printer assembly on the [Discord channel](https://discord.gg/4RNmUT7A5G)!

### First print
You can run a first test print, using the slicer template included in the "Software" folder. The template is for [ORCA Slicer](https://github.com/SoftFever/OrcaSlicer) since that is currently shaping up to be the best open-source slicer if you're not using Prusa's printers. PrusaSlicer and SuperSlicer are also great, of course, but you should be fine with ORCA.
* BTW, download ORCA slicer from the official Github rather than the weird .net/.org domain names that appear online. IIRC some of these are fake or malicious.

# Post-setup tuning

### REQUIRED: Input shaping calibration
After completing the build you should also tune input shaping using [the official guide](https://www.klipper3d.org/Measuring_Resonances.html). Note we are using the ADXL345 for this, unless you have a different toolhead board which comes with an in-built one (like the LDO Picobilical, for instance).

### REQUIRED: Determining max accelerations and speeds
You should then also determine the maximum acceleration and speed using [Ellis' guide](https://ellis3dp.com/Print-Tuning-Guide/articles/determining_max_speeds_accels.html). Note we have already included his TEST_SPEED macro in our default template bundle.
* As he states, you'll probably want to run everyday prints at around 80-85% of the max acceleration and limit, to avoid issues.
* You will likely mainly notice issues with excessive max speed, at some point the toolhead will start crashing into the frame so be careful.

### OPTIONAL: General printer tuning
You should be good to go using the default print slicer template + the pressure advance values which we have included in the config.
* If you require further tuning of these parameters, or other aspects of the printer, [Ellis' guide](https://ellis3dp.com/Print-Tuning-Guide/articles/index_tuning.html) is a well-known resource with tutorials that help to better understand the basics, as well as some more advanced concepts.
* Your extruder flow rate might need calibration, but in our experience the default value of around 111% to 114% with this extruder/hotend combo.

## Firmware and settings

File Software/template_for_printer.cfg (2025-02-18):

[include mainsail.cfg]
[include macros.cfg]
# [include timelapse.cfg]

# This file contains common pin mappings for the BIGTREETECH SKR Pico V1.0
# To use this config, the firmware should be compiled for the RP2040 with
# USB communication.

# The "make flash" command does not work on the SKR Pico V1.0. Instead,
# after running "make", copy the generated "out/klipper.uf2" file
# to the mass storage device in RP2040 boot mode

## Voron Design VORON 0.2 SKR Pico V1.0 config

## *** THINGS TO CHANGE/CHECK: ***
## MCU path                                                                     [mcu] section
## Z and Extruder motor currents                                                [tmc2209 stepper_*] sections. Uncomment the stepper motor you have
## Full steps per rotation for Extruder                                         [extruder] section
## Thermistor types                                                             [extruder] and [heater_bed] sections - See https://www.klipper3d.org/Config_Reference.html#common-thermistors for common thermistor types
## Motor currents                                                               [extruder] [stepper] and [_HOME_X/Y] macro sections
## PID tune                                                                     [extruder] and [heater_bed] sections
## Fine tune E steps                                                            [extruder] section
## For more info                                                                check https://docs.vorondesign.com/build/startup/#v0


[mcu]
#####################################################################
# Obtain definition by "ls -l /dev/serial/by-id/"
#####################################################################
serial: /dev/serial/by-id/usb-Klipper_rp2040_someextralettersandnumbers-if00
## serial: /dev/ttyAMA0 											# for UART connection
restart_method: command

[mcu rpi]
serial: /tmp/klipper_host_mcu

[adxl345]
cs_pin: rpi:None

[resonance_tester]
accel_chip: adxl345
probe_points:
    60, 60, 20  # an example

[temperature_sensor mcu_temp]
sensor_type: temperature_mcu
min_temp: 0
max_temp: 100

[temperature_sensor raspberry_pi]
sensor_type: temperature_host
min_temp: 10
max_temp: 100

[printer]
kinematics: corexy
max_velocity: 500
max_accel: 10000
max_z_velocity: 15
max_z_accel: 45
square_corner_velocity: 6.0

#####################################################################
#      X/Y Stepper Settings
#####################################################################

[stepper_x]
step_pin: gpio11
## Refer to https://docs.vorondesign.com/build/startup/#v0
dir_pin: gpio10                                                     # Check motor direction in link above. If inverted, add a ! before gpio10
enable_pin: !gpio12
rotation_distance: 40
microsteps: 32
full_steps_per_rotation: 200                                        # Set to 400 for 0.9° degree stepper motor, 200 is for 1.8° stepper motors
endstop_pin: tmc2209_stepper_x:virtual_endstop
position_endstop: 120
position_max: 120
homing_speed: 40                                                   
homing_retract_dist: 0
homing_positive_dir: true

[tmc2209 stepper_x]
uart_pin: gpio9
tx_pin: gpio8
uart_address: 0
interpolate: False
run_current: 0.5
# you need to calculate the run_current value using the equation (rated_motor_current * 0.707 = Maximum_run_current) start with a value that is about 60%-70% of your maximum value.
sense_resistor: 0.110
stealthchop_threshold: 0                                            # Set to 999999 to turn stealthchop on, and 0 to use spreadcycle
diag_pin: ^gpio4    												# YOU NEED TO JUMP THIS DIAG PIN ON YOUR BOARD FOR SENSORLESS HOMING TO WORK 
driver_SGTHRS: 92  												# this is set to 255 which is the MAX sensitivity for sensorless homing, you will need to tune this later
# 40 homing speed: 114 max, 75 min, 94 ish halfway

[stepper_y]
step_pin: gpio6
## Refer to https://docs.vorondesign.com/build/startup/#v0
dir_pin: gpio5                                                      # Check motor direction in link above. If inverted, add a ! before gpio5
enable_pin: !gpio7
rotation_distance: 40
microsteps: 32
full_steps_per_rotation: 200                                        # Set to 400 for 0.9° degree stepper motor, 200 is for 1.8° stepper motors
endstop_pin: tmc2209_stepper_y:virtual_endstop
position_endstop: 120
position_max: 120
homing_speed: 40                                                     
homing_retract_dist: 0
homing_positive_dir: true

[tmc2209 stepper_y]
uart_pin: gpio9
tx_pin: gpio8
uart_address: 2
interpolate: False
run_current: 0.5
# you need to calculate the run_current value using the equation (rated_motor_current * 0.707 = Maximum_run_current) start with a value that is about 60%-70% of your maximum value.
sense_resistor: 0.110
stealthchop_threshold: 0                                            # Set to 999999 to turn stealthchop on, and 0 to use spreadcycle
diag_pin: ^gpio3    												# YOU NEED TO JUMP THIS DIAG PIN ON YOUR BOARD FOR SENSORLESS HOMING TO WORK 
driver_SGTHRS: 94 												# this is set to 255 which is the MAX sensitivity for sensorless homing, you will need to tune this later
# 40 homing speed: 107 max, 84 min, 95 ish halfway

#####################################################################
#   Z Stepper Settings
#####################################################################

[stepper_z]
step_pin: gpio19
dir_pin: !gpio28                                                    # Remove the ! before gpio28 if motor direction is inverted.
enable_pin: !gpio2
rotation_distance: 8                                                # For T8x8 integrated lead screw
microsteps: 32
endstop_pin: ^gpio25
#position_endstop: 120
position_max: 120
position_min: -1.5
homing_speed: 10
second_homing_speed: 3.0
homing_retract_dist: 3.0


[tmc2209 stepper_z]
uart_pin: gpio9
tx_pin: gpio8
uart_address: 1
interpolate: False
## For OMC (StepperOnline) 17LS13-0404E-200G 0.4A 
#run_current: 0.2
## For LDO-42STH25-1004CL200E 1.0A
run_current: 0.37
sense_resistor: 0.110
stealthchop_threshold: 0                                            # Set to 999999 to turn stealthchop on, and 0 to use spreadcycle

#####################################################################
#   Extruder
#####################################################################

[extruder]
step_pin: gpio14
dir_pin: !gpio13                                                     # Add ! if moving opposite direction
enable_pin: !gpio15
full_steps_per_rotation: 200 # 360/1.8sd                           # Set to 200 for LDO 1.8° stepper motor, and set to 400 for OMC(StepperOnline) 0.9° stepper motor
rotation_distance: 4.5714 # (200fsprx16ms)/700spmm                 # See calibrating rotation_distance on extruders doc
# gear_ratio: 50:10                                                   # For Mini Afterburner
# gear_ratio: 75:10                                                   # For Orbiter F2.85 (but leave this commented out to avoid overwriting rotation_distance effect)
microsteps: 16
nozzle_diameter: 0.400
filament_diameter: 2.850
# heater_pin: gpio23
heater_pin: gpio21 # replacing to here; I think I may have damaged the io23 MOSFET due to using a 70W heater 
## Check what thermistor type you have. See https://www.klipper3d.org/Config_Reference.html#common-thermistors for common thermistor types.
## Use "Generic 3950" for NTC 100k 3950 thermistors
# sensor_type: ATC Semitec 104GT-2
sensor_type: Generic 3950
sensor_pin: gpio27
#control: pid                                                        # Do PID calibration after initial checks
#pid_Kp: 28.182
#pid_Ki: 1.978
#pid_Kd: 100.397
min_temp: 0
max_temp: 270
min_extrude_temp: 200
max_extrude_only_distance: 150
max_extrude_cross_section: 0.8
pressure_advance: 1.25                                               # See tuning pressure advance doc
pressure_advance_smooth_time: 0.020
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

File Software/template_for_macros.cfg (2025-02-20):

[gcode_macro PRINT_START]
#   Use PRINT_START for the slicer starting script - please customize for your slicer of choice
gcode:
    {% set EXTRUDER_TEMP = params.EXTRUDER|default(225)|float %} ; parse i/p argument
    G28                            ; home all axes
    G90                            ; absolute positioning    
    G1 Z20 F3000                   ; move nozzle away from bed
    G1 X60 Y100 F3600          ; park nozzle at rear to prevent oozing over center
    SET_GCODE_OFFSET Z=0 MOVE=1 ; reset z offset to prevent stacking after each print
    M109 S{EXTRUDER_TEMP} ; wait for nozzle to heat up
    # HYPERLAPSE CYCLE=1 ACTION=START ; if using timelapse via Crowsnest
   
[gcode_macro PRINT_END]
#   Use PRINT_END for the slicer ending script - please customize for your slicer of choice
gcode:
    M400                           ; wait for buffer to clear
    G92 E0                         ; zero the extruder
    G1 E-4.0 F3600                 ; retract filament
    G91                            ; relative positioning

    #   Get Boundaries
    {% set max_x = printer.configfile.config["stepper_x"]["position_max"]|float %}
    {% set max_y = printer.configfile.config["stepper_y"]["position_max"]|float %}
    {% set max_z = printer.configfile.config["stepper_z"]["position_max"]|float %}

    #   Check end position to determine safe direction to move
    {% if printer.toolhead.position.x < (max_x - 20) %}
        {% set x_safe = 20.0 %}
    {% else %}
        {% set x_safe = -20.0 %}
    {% endif %}

    {% if printer.toolhead.position.y < (max_y - 20) %}
        {% set y_safe = 20.0 %}
    {% else %}
        {% set y_safe = -20.0 %}
    {% endif %}

    {% if printer.toolhead.position.z < (max_z - 2) %}
        {% set z_safe = 2.0 %}
    {% else %}
        {% set z_safe = max_z - printer.toolhead.position.z %}
    {% endif %}

    G0 Z{z_safe} F3600             ; move nozzle up
    G0 X{x_safe} Y{y_safe} F20000  ; move nozzle to remove stringing
    TURN_OFF_HEATERS
    M107                           ; turn off fan
    G90                            ; absolute positioning
    G0 X60 Y{max_y-10} Z105 F3600          ; park nozzle at rear
    G4 S20 ; wait a bit to record a few frames after the print is finished
    # HYPERLAPSE CYCLE=1 ACTION=STOP ; if using timelapse via Crowsnest


[gcode_macro FRONT]
description: Raises the bed, and moves the toolhead to the front to allow easy access for maintenance, etc.
gcode:
  {% set x_center = printer.toolhead.axis_maximum.x|float / 2.0 %}
  {% set y_center = printer.toolhead.axis_maximum.y|float / 2.0 %}
  G90
  G1 Z105 F3000 
  G1 X{x_center} Y0 F7800


[gcode_macro NOZZLE_PURGE]
description: Draw a purge line at the front left edge of the build plate. Recommended to run before each print to prime the nozzle for printing.
gcode:
  M106 S255 ; enable fans
  G0 X5 Y118 F3000 ; Go to back
  G0 Z0.2 F300; Drop to bed
  M83 ; Set extruder to relative mode
  # G1 X45 E8 F1200 ; Extrude 25mm of filament in a 4cm line
  G1 X105 E8.46 F300 ; extruder  
  G1 Y117.6 F3000 ; go to the side a little
  G1 X5 E8.46 F300 ;extrude line on the way back
  G1 Y117.2 F3000 ; go to the side a little
  G1 Z0.5 F300; Raise and begin printing.


[gcode_macro CENTER]
description: Moves the toolhead to the center
gcode:
  CHOME
  {% set x_center = printer.toolhead.axis_maximum.x|float / 2.0 %}
  {% set y_center = printer.toolhead.axis_maximum.y|float / 2.0 %}
  G90
  G1 X{x_center} Y{x_center} F7800

[gcode_macro FANS_MAX]
description: Turn print fans to 100%
gcode:
  M106 S255

[gcode_macro FANS_OFF]
description: Turn print fans to 0%
# turn print fans to 100%
gcode:
  M106 S0


[gcode_macro TEST_SPEED]
gcode:
    # Speed
    {% set speed  = params.SPEED|default(printer.configfile.settings.printer.max_velocity)|int %}
    # Iterations
    {% set iterations = params.ITERATIONS|default(5)|int %}
    # Acceleration
    {% set accel  = params.ACCEL|default(printer.configfile.settings.printer.max_accel)|int %}
    # Bounding inset for large pattern (helps prevent slamming the toolhead into the sides after small skips, and helps to account for machines with imperfectly set dimensions)
    {% set bound = params.BOUND|default(20)|int %}
    # Size for small pattern box
    {% set smallpatternsize = SMALLPATTERNSIZE|default(20)|int %}
    
    # Large pattern
        # Max positions, inset by BOUND
        {% set x_min = printer.toolhead.axis_minimum.x + bound %}
        {% set x_max = printer.toolhead.axis_maximum.x - bound %}
        {% set y_min = printer.toolhead.axis_minimum.y + bound %}
        {% set y_max = printer.toolhead.axis_maximum.y - bound %}
    
    # Small pattern at center
        # Find X/Y center point
        {% set x_center = (printer.toolhead.axis_minimum.x|float + printer.toolhead.axis_maximum.x|float ) / 2 %}
        {% set y_center = (printer.toolhead.axis_minimum.y|float + printer.toolhead.axis_maximum.y|float ) / 2 %}
        
        # Set small pattern box around center point
        {% set x_center_min = x_center - (smallpatternsize/2) %}
        {% set x_center_max = x_center + (smallpatternsize/2) %}
        {% set y_center_min = y_center - (smallpatternsize/2) %}
        {% set y_center_max = y_center + (smallpatternsize/2) %}

    # Save current gcode state (absolute/relative, etc)
    SAVE_GCODE_STATE NAME=TEST_SPEED
    
    # Output parameters to g-code terminal
    { action_respond_info("TEST_SPEED: starting %d iterations at speed %d, accel %d" % (iterations, speed, accel)) }
    
    # Home and get position for comparison later:
        M400 # Finish moves - https://github.com/AndrewEllis93/Print-Tuning-Guide/issues/66
        G28
        # QGL if not already QGLd (only if QGL section exists in config)
        {% if printer.configfile.settings.quad_gantry_level %}
            {% if printer.quad_gantry_level.applied == False %}
                QUAD_GANTRY_LEVEL
                G28 Z
            {% endif %}
        {% endif %} 
        # Move 50mm away from max position and home again (to help with hall effect endstop accuracy - https://github.com/AndrewEllis93/Print-Tuning-Guide/issues/24)
        G90
        G1 X{printer.toolhead.axis_maximum.x-50} Y{printer.toolhead.axis_maximum.y-50} F{30*60}
        M400 # Finish moves - https://github.com/AndrewEllis93/Print-Tuning-Guide/issues/66
        G28 X Y
        G0 X{printer.toolhead.axis_maximum.x-1} Y{printer.toolhead.axis_maximum.y-1} F{30*60}
        G4 P1000 
        GET_POSITION

    # Go to starting position
    G0 X{x_min} Y{y_min} Z{bound + 10} F{speed*60}

    # Set new limits
    SET_VELOCITY_LIMIT VELOCITY={speed} ACCEL={accel} ACCEL_TO_DECEL={accel / 2}

    {% for i in range(iterations) %}
        # Large pattern diagonals
        G0 X{x_min} Y{y_min} F{speed*60}
        G0 X{x_max} Y{y_max} F{speed*60}
        G0 X{x_min} Y{y_min} F{speed*60}
        G0 X{x_max} Y{y_min} F{speed*60}
        G0 X{x_min} Y{y_max} F{speed*60}
        G0 X{x_max} Y{y_min} F{speed*60}
        
        # Large pattern box
        G0 X{x_min} Y{y_min} F{speed*60}
        G0 X{x_min} Y{y_max} F{speed*60}
        G0 X{x_max} Y{y_max} F{speed*60}
        G0 X{x_max} Y{y_min} F{speed*60}
    
        # Small pattern diagonals
        G0 X{x_center_min} Y{y_center_min} F{speed*60}
        G0 X{x_center_max} Y{y_center_max} F{speed*60}
        G0 X{x_center_min} Y{y_center_min} F{speed*60}
        G0 X{x_center_max} Y{y_center_min} F{speed*60}
        G0 X{x_center_min} Y{y_center_max} F{speed*60}
        G0 X{x_center_max} Y{y_center_min} F{speed*60}
        
        # Small patternbox
        G0 X{x_center_min} Y{y_center_min} F{speed*60}
        G0 X{x_center_min} Y{y_center_max} F{speed*60}
        G0 X{x_center_max} Y{y_center_max} F{speed*60}
        G0 X{x_center_max} Y{y_center_min} F{speed*60}
    {% endfor %}

    # Restore max speed/accel/accel_to_decel to their configured values
    SET_VELOCITY_LIMIT VELOCITY={printer.configfile.settings.printer.max_velocity} ACCEL={printer.configfile.settings.printer.max_accel} ACCEL_TO_DECEL={printer.configfile.settings.printer.max_accel / 2} 

    # Re-home and get position again for comparison:
        M400 # Finish moves - https://github.com/AndrewEllis93/Print-Tuning-Guide/issues/66
        G28 # This is a full G28 to fix an issue with CoreXZ - https://github.com/AndrewEllis93/Print-Tuning-Guide/issues/12
        # Go to XY home positions (in case your homing override leaves it elsewhere)
        G90
        G0 X{printer.toolhead.axis_maximum.x-1} Y{printer.toolhead.axis_maximum.y-1} F{30*60}
        G4 P1000 
        GET_POSITION

    # Restore previous gcode state (absolute/relative, etc)
    RESTORE_GCODE_STATE NAME=TEST_SPEED
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

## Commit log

2025-02-19 Update BOM.
    [BOM_Flex_Printer.ods]
2025-02-20 Update macro.cfg template
    [template_for_macros.cfg]
